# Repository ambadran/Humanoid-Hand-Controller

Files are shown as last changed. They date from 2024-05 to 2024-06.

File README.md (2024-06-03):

# Humanoid-Hand-Controller

Interfacing muscle sensor V2 using micropython code 

(OPTIONAL BUT RECOMMENDED: Use AD7705 16-bit ADC to give more resolution and muscle activity range to play with)

The idea is to program a sequence of muscle intensities at specific time intervals which correlate to a specific `Movmement` python object

This `Movement` object can then be mapped to any actual transducer action you like. 

In this library it is assumed that the transducer is 5 servo motors each controlling a finger.

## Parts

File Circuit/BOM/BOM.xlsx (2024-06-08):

No. | Name | Cost | Quantity | Total Cost | Description | Store
1 | 18650 Batteries | 70 | 4 | 280 | 12v power supply and 1 extra for seperate power supply
2 | 3s BMS | 100 | 1 | 100
3 | Buck Converter | 55 | 1 | 55
4 | Boost Converter | 45 | 1
5 | Wires | 10 | 0.3 | 3
6 | Resistors | 0.75 | 3 | 2.25 | 10k x3
7 | Tl072 OpAmp | 10 | 1 | 10
8 | IC Socket DIP8 | 1 | 1 | 1 | for TL072
9 | Crystal Oscillator 4Mhz | 5 | 1 | 5
10 | Pin Header Female 1x3 | 1 | 2 | 2 | Muscle Sensor Power
11 | Pin Header Female 1x2 | 1 | 1 | 1 | Muscle Sensor Signal
12 | Pin Header Female 1x20 | 5 | 2 | 10 | for Raspberry Pi Pico
13 | Raspberry Pi Pico | 0 | 1 | 0 | ALREADY BOUGHT
14 | AD7705 IC | 0 | 1 | 0 | ALREADY BOUGHT
15 | IC Socket DIP16 | 2 | 1 | 2 | for AD7705 IC
16 | GX16 – 8Pole connector | 60 | 1 | 60 | for servo output
17 | JST 2-pin | 0.75 | 1 | 0.75 | for Power12v Input
18 | Capacitor 10nF | 0.5 | 1 | 0.5
19 | Capacitor 330uF | 2.5 | 1 | 2.5
20 | Linear Regulator 3.3v LD33v | 25 | 1 | 25
21 | PCB | 140 | 1 | 140
22 | OLED SSD1306 128x64 | 250 | 1 | 250
23 | Power Switch 2P2T | 17 | 1 | 17
24 | 3D Prints | 2.5 | 165 | 412.5 | Box + Cover + wrist mount
25 | Terminals | 1 | 4 | 4
26 | Button | 10 | 1 | 10
27 | JST 4-Pin Male and Female pair | 5 | 1 | 5
<> | Design, Manufacture and Testing |  |  | 5800
 | TOTAL |  |  | 7198.5
 |  |  |  |  |  |  | 3d print
 |  |  |  |  |  |  | oled
 |  |  |  |  |  |  | main.py
 |  |  |  |  |  |  | battery welding

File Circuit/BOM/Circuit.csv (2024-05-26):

Id | Designator | Footprint | Quantity | Designation | Supplier and ref
1 | R1,R3,R2 | R_Axial_DIN0207_L6.3mm_D2.5mm_P7.62mm_Horizontal | 3 | 10k
2 | U1 | DIP-8_W7.62mm_Socket_LongPads | 1 | TL072
3 | Y1 | Crystal_HC49-4H_Vertical | 1 | Crystal
4 | MuscleSensor_PowerInput1 | PinSocket_1x03_P2.54mm_Vertical | 1 | Conn_01x03
5 | J1,J2 | PinSocket_1x20_P2.54mm_Vertical | 2 | Conn_01x20
6 | Signal_Input1 | PinSocket_1x02_P2.54mm_Vertical | 1 | Conn_01x02
7 | AD7705 | DIP-16_W7.62mm_LongPads | 1 | Conn_02x08_Counter_Clockwise
8 | MuscleSensor_PowerInput2 | JST_EH_S3B-EH_1x03_P2.50mm_Horizontal | 1 | Conn_01x03
9 | ServoOutput1 | JST_EH_B8B-EH-A_1x08_P2.50mm_Vertical | 1 | Conn_01x08
10 | C2 | CP_Radial_D8.0mm_P3.80mm | 1 | 330uF
11 | U2 | TO-220-3_Vertical | 1 | AMS1117-3.3
12 | C3 | C_Disc_D5.0mm_W2.5mm_P5.00mm | 1 | 10nF
13 | Power12V1 | JST_EH_B2B-EH-A_1x02_P2.50mm_Vertical | 1 | Conn_01x02

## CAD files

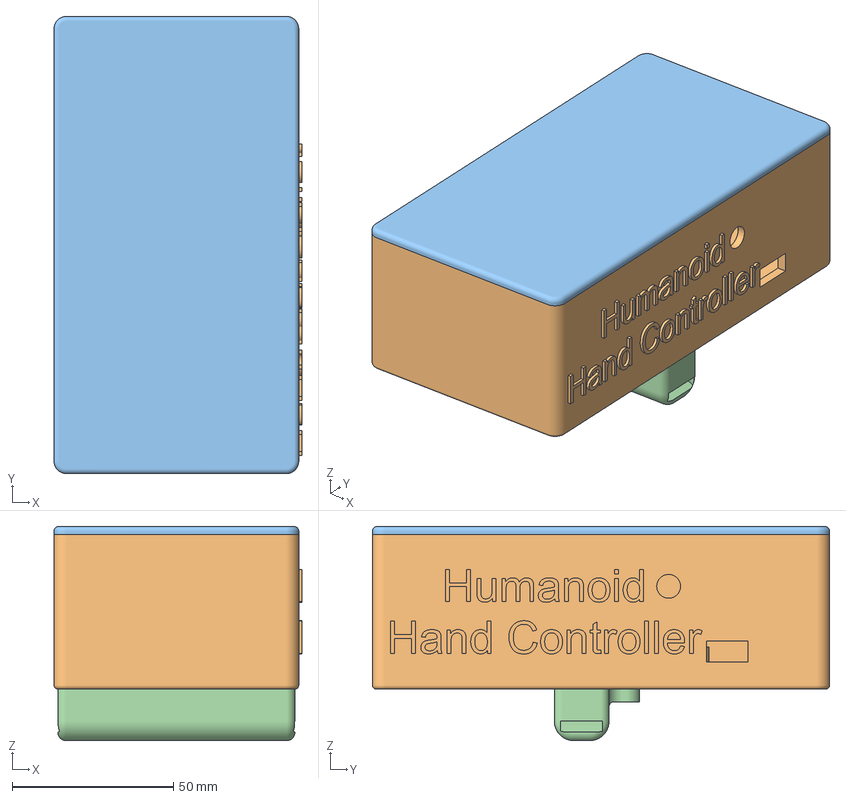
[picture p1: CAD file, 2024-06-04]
Mechanics/Humanoid-Hand-Controller.3mf
77.0 x 142.0 x 66.5 mm
GX16_Cover_Slot
Main_Body
Top_Cover
Wrist_mount

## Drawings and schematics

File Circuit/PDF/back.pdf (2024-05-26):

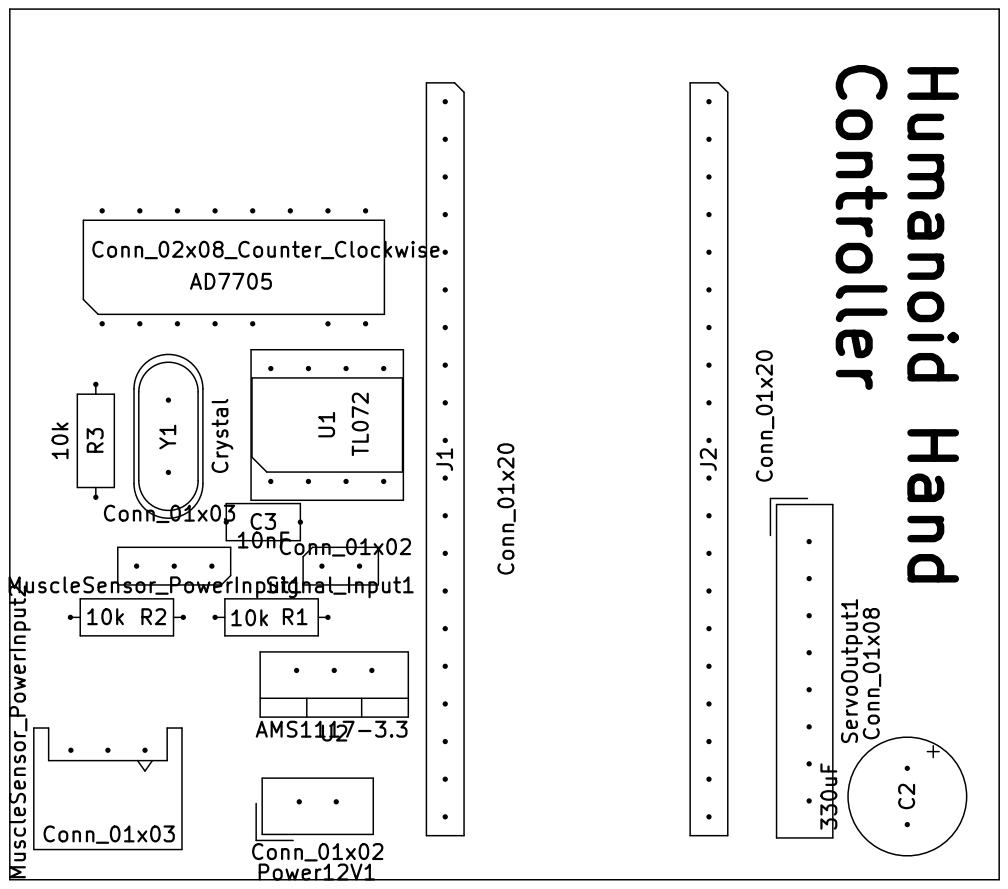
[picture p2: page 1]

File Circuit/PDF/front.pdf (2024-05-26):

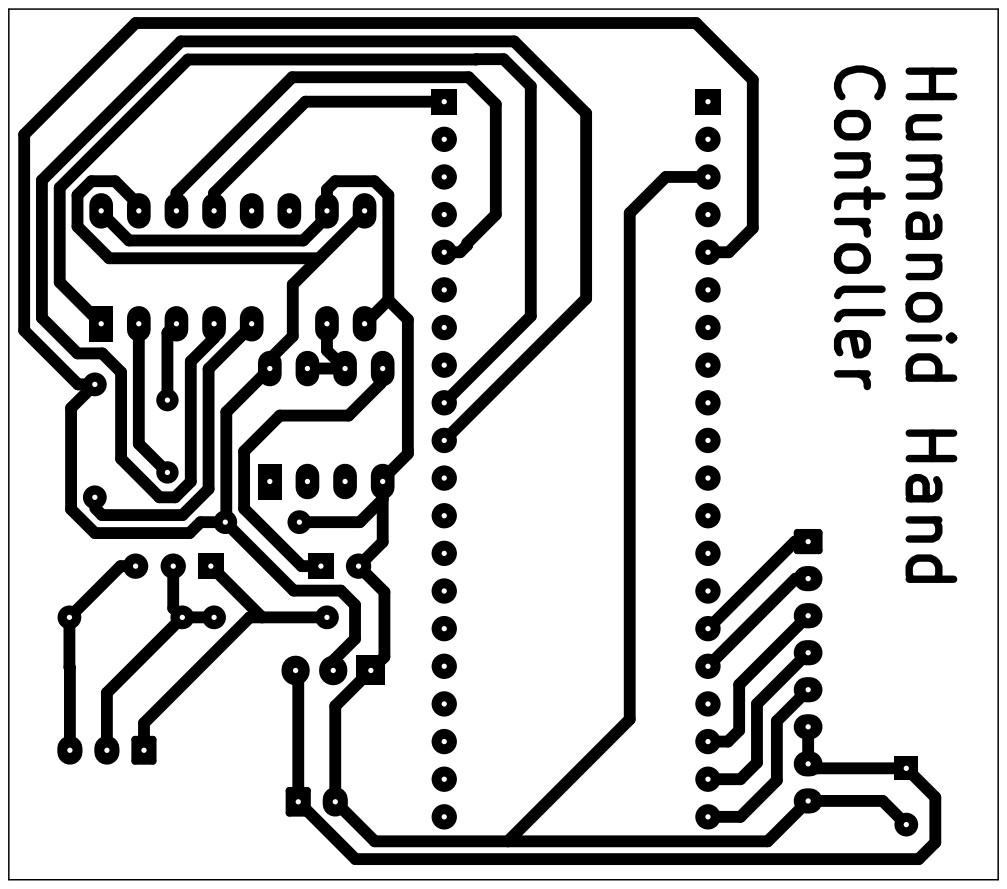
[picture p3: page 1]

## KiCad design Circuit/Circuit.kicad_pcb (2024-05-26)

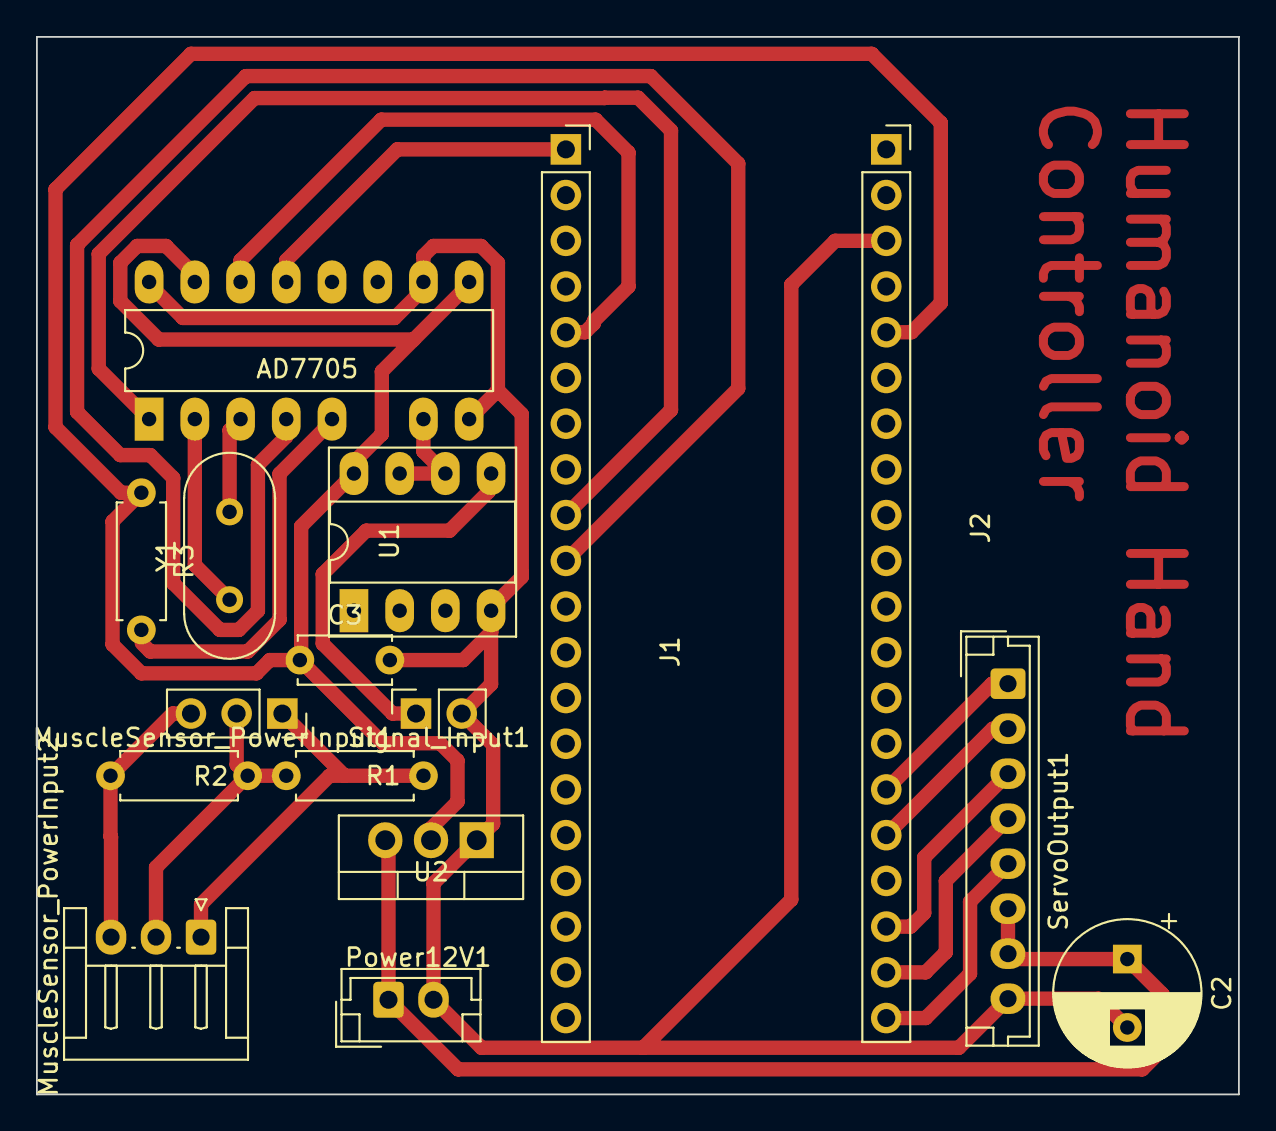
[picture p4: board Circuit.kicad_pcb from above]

Board: 2 copper layers, 66.8 x 58.8 mm, 16 parts (0 on the bottom side), 20 nets.

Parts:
AD7705: Conn_02x08_Counter_Clockwise; DIP-16_W7.62mm_LongPads
C2: 330uF; CP_Radial_D8.0mm_P3.80mm
C3: 10nF; C_Disc_D5.0mm_W2.5mm_P5.00mm
J1, J2: Conn_01x20; PinSocket_1x20_P2.54mm_Vertical
MuscleSensor_PowerInput1: Conn_01x03; PinSocket_1x03_P2.54mm_Vertical
MuscleSensor_PowerInput2: Conn_01x03; JST_EH_S3B-EH_1x03_P2.50mm_Horizontal
Power12V1: Conn_01x02; JST_EH_B2B-EH-A_1x02_P2.50mm_Vertical
R1, R2, R3: 10k; R_Axial_DIN0207_L6.3mm_D2.5mm_P7.62mm_Horizontal
ServoOutput1: Conn_01x08; JST_EH_B8B-EH-A_1x08_P2.50mm_Vertical
Signal_Input1: Conn_01x02; PinSocket_1x02_P2.54mm_Vertical
U1: TL072; DIP-8_W7.62mm_Socket_LongPads
U2: AMS1117-3.3; TO-220-3_Vertical
Y1: Crystal; Crystal_HC49-4H_Vertical

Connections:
+3.3V: AD7705.9, AD7705.15, C3.1, J2.5, R3.1, U1.8 (V+), U2.2 (VO)
+12V: C2.1, Power12V1.1, ServoOutput1.6, ServoOutput1.7, U2.3 (VI)
+24V: MuscleSensor_PowerInput1.3, MuscleSensor_PowerInput2.3, R2.2
CS: AD7705.4, J1.10
GND: AD7705.8, AD7705.10, AD7705.16, C2.2, C3.2, J2.3, Power12V1.2, ServoOutput1.8, Signal_Input1.2, U1.4 (V-), U2.1 (GND)
GNDA: MuscleSensor_PowerInput1.1, MuscleSensor_PowerInput2.1, R1.1
MISO: AD7705.13, J1.1
MOSI: AD7705.14, J1.5
MuscleSensor_Signal: Signal_Input1.1, U1.5 (+)
MuscleSensor_Signal_OpAmp: AD7705.7, U1.6 (-), U1.7
unnamed: AD7705.2, Y1.1
unnamed: AD7705.3, Y1.2
unnamed: AD7705.5, R3.2
unnamed: MuscleSensor_PowerInput1.2, MuscleSensor_PowerInput2.2, R1.2, R2.1
SCLK: AD7705.1, J1.9
Servo1: J2.15, ServoOutput1.1
Servo2: J2.16, ServoOutput1.2
Servo3: J2.18, ServoOutput1.3
Servo4: J2.19, ServoOutput1.4
Servo5: J2.20, ServoOutput1.5

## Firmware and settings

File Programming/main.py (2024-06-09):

from muscle_sensor import read_contraction_and_execute, muscle, ad
from machine import Pin, Timer
import time
from micropython import const

FIRST_COMMAND_DELAY_TIME = const(300)
SECOND_COMMAND_DELAY_TIME = const(1000)
THIRD_COMMAND_DELAY_TIME = const(2000)

def main():
    '''
    Main Routine
    '''
    # BUTTON IS ACTIVE LOW
    button = Pin(22, Pin.IN, Pin.PULL_DOWN)
    button_pressed = False
    led = Pin(25, Pin.OUT)

    timer = Timer(period=500, mode=Timer.PERIODIC, callback=lambda t:led.value(not led.value()))

    try:
        while True:
            while not button.value():
                if not button_pressed:
                    start = time.ticks_ms()
                    button_pressed = True

            if button_pressed:
                if time.ticks_diff(time.ticks_ms(), start) <= FIRST_COMMAND_DELAY_TIME:

                    # Keep reading untill the next sequence
                    while True:
                        read_contraction_and_execute()
                        time.sleep(1)

                elif time.ticks_diff(time.ticks_ms(), start) <= SECOND_COMMAND_DELAY_TIME:
                    muscle.calibrate_muscle_intensity_ranges()

                # elif time.ticks_diff(time.ticks_ms(), start) <= THIRD_COMMAND_DELAY_TIME:
                else:  ## until I want to add another command
                    muscle.test_ad(5)  # persistently print ad values for 5 seconds

                #TODO: make a default screen to appear after each function
                # MuscleSensorStatus.report_saved_movements(hum)

                button_pressed = False

    except Exception as e:
        print("Error: ", e)

    finally:
        timer.deinit()
        led.off()



main()

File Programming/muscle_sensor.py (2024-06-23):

from ad7705 import ad
import time
from machine import Timer, Pin, I2C
from servo import Servo
import ssd1306
  

class Movement:
    '''
    A specific muscle movement consists of a specific muscle contractions in a specific order with specific intervals between each muscle contraction. 
    '''
    MAXIMUM_NUM_INTENSITIES = 3
    def __init__(self, muscle_intensities: tuple[MuscleIntensity], times: tuple[int]):
        '''
        muscle_intensities: the values that would be read in `times` periods

        OBVIOUS FACT: the MuscleIntensity at time0 must NEVER BE NONE
        '''
        #TODO: check muscle_intensities and times datatypes
        if len(muscle_intensities) != len(times):
            raise ValueError("number of adc_values given must equal number of times given")

        # moving adc values and times into one list where every value is 
        self.muscle_intensities_order = [0 for _ in range(times[-1]+1)]
        for n in range(len(times)):
            self.muscle_intensities_order[times[n]] = muscle_intensities[n]
        self.muscle_intensities_order = tuple(self.muscle_intensities_order)

class Finger:
    MINIMUM_DEGREE = 0
    MAXIMUM_DEGREE = 120
    def __init__(self, servo_pin: int, movement: Movement):
        self._servo = Servo(pin_id=servo_pin)
        self.movement = movement
        self.contraction_off()

    @property
    def contraction_value(self):
        return self._servo.read()

    @contraction_value.setter
    def contraction_value(self, value):
        self._servo.write(value)

    def contraction_full(self):
        self._servo.write(self.MAXIMUM_DEGREE)

    def contraction_off(self):
        self._servo.write(self.MINIMUM_DEGREE)

    def contraction_toggle(self):
        if self.contraction_value:
            self._servo.write(self.MINIMUM_DEGREE)
        else:
            self._servo.write(self.MAXIMUM_DEGREE)

class HumanoidHand:

    # ssd1306 display
    display = ssd1306.SSD1306_I2C(128, 64, I2C(1, scl=Pin(27), sda=Pin(26)))
 
    def __init__(self, fingers: tuple[Finger], full_palm_movement: Movement):

        if len(fingers) != 5:
            raise ValueError("finger tuple must be 5 values!")

        self.fingers = fingers
        self.finger1 = fingers[0]
        self.finger2 = fingers[1]
        self.finger3 = fingers[2]
        self.finger4 = fingers[3]
        self.finger5 = fingers[4]
        self.full_palm_movement = full_palm_movement

    def movement_tuple(self) -> tuple[Movement]:
        '''
        return tuple of Movement in order of fingers from 1 to 5
        very important for MuscleSensor to detect what finger is it
        '''
        movements = []
        for finger in self.fingers:
            movements.append(finger.movement)

        movements.append(self.full_palm_movement)
        return movements

    def finger_test(self):
        '''
        tests each individual fingers
        '''
        for finger_ind in range(5):
            MuscleSensorStatus.report_custom(f"Testing finger:{finger_ind}!")
            self.fingers[finger_ind].contraction_toggle()
            time.sleep(1)
            self.fingers[finger_ind].contraction_toggle()
            time.sleep(1)

    def full_palm_contract(self):
        '''
        contracts all palm fingers
        '''
        for finger in self.fingers:
            finger.contraction_full()
            time.sleep(2)

    def full_palm_relax(self):
        '''
        contracts all palm fingers
        '''
        for finger in self.fingers:
            finger.contraction_off()

    def full_palm_toggle(self):
        '''
        toggle all palm fingers
        '''
        for finger in self.fingers:
            finger.contraction_toggle()
            time.sleep(2)

class MuscleSensorStatus:
    PENDING_ACTIVIITY = "PENDING_ACTIVIITY" 
    READ_IN_PROGRESS =  "READ_IN_PROGRESS" 
    MOVEMENT_DETECTED = "MOVEMENT_DETECTED" 
    MOVEMENT_INVALID =  "MOVEMENT_INVALID" 
    IDLE ="IDLE" 

    @classmethod
    def report_full(cls, muscle: MuscleSensor):
        '''
        prints full report in terminal and on ssd1306 screen
        '''
        print(f"{muscle.status}: Muscle Intensity: {muscle.muscle_intensities_order} @ time: {muscle.current_time} ", end=' \r')
        HumanoidHand.display.fill(0)
        HumanoidHand.display.text(muscle.status, 0, 0, 1)
        HumanoidHand.display.text(str(muscle.muscle_intensities_order), 0, 12, 1)
        HumanoidHand.display.text(f"time: {muscle.current_time}", 0, 24, 1)
        HumanoidHand.display.show()

        time.sleep_us(100)

    @classmethod
    def report_status(cls, muscle: MuscleSensor):
        '''
        print status in terminal and ssd1306
        '''
        print(muscle.status)
        HumanoidHand.display.text(muscle.status, 0, 0, 1)
        HumanoidHand.display.show()
        time.sleep_us(100)

    @classmethod
    def report_saved_movements(cls, movements: list[Movement]):
        '''
        prints the saved movements on the screen
        '''
        print(f"Defined Moves:")  # unfortionately can't display this and the 5 movement in the oled screen at once :(
        for ind, movement in enumerate(movements):
            MuscleSensorStatus.report_custom(f"M{ind+1}: {movement.muscle_intensities_order}", clear_display=False, line=ind*12)

    @classmethod
    def report_ad(cls):
        '''
        prints in terminal and ssd1306 the ad values
        '''
        global ad
        ad_value = ad.readADResultRaw()
        print(f"Reading: {ad_value}", end=' \r')
        HumanoidHand.display.fill(0)
        HumanoidHand.display.text(f"AD7705: {ad_value}", 0, 0, 1)
        HumanoidHand.display.show()
        time.sleep_us(100)

    @classmethod
    def report_custom(cls, string, clear_display:bool=True, clear_line: bool=False, line: int=0, ending: str='\n'):
        '''
        display custome message in oled and terminal
        AFTER deleting the whole screen
        '''
        print(string, end=ending)

        if clear_display:
            HumanoidHand.display.fill(0)
        if clear_line:
            # very useful to simulate '\r' like functionality in terminal
            HumanoidHand.display.fill_rect(72, line, 127, 20, 0)

        #TODO: write an algorithm to split text into words then print the most words possible
        #       in the 16 character wide space per line available
        HumanoidHand.display.text(string, 0, line, 1)
        HumanoidHand.display.show()
        time.sleep_us(100)


'''
holding tuples values of upper and lower bound

Listed from lowest intensity to highest intensity
'''
class MuscleIntensity:
    NONE = 0
    LOW = 1
    MEDIUM = 2
    HIGH = 3
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

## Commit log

2024-05-25 finished PCB design, pending final distance measurements
    [Circuit.kicad_pcb, Circuit.kicad_sch]
2024-05-25 added BOM
    [BOM.xlsx]
2024-05-26 final PCB design done
    [BOM.xlsx, Circuit.csv, Circuit.kicad_pcb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]
2024-05-26 BOM done and minor changes
    [BOM.xlsx, Circuit.kicad_sch]
2024-05-28 added calibration algorithm
2024-06-02 added a switch and main.py to be work completly without a computer now
2024-06-04 added pcb step file
2024-06-04 finished 3D model of controller box with write mount
    [Humanoid-Hand-Controller.3mf]
2024-06-08 added new BOM
    [BOM.xlsx]
2024-06-09 added a view raw ad value function by pressing button more than 1sec
2024-06-23 added delay for full hand contract function between each finger
